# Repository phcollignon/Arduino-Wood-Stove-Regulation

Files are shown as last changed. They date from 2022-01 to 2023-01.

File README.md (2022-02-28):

# Arduino Wood Stove Regulator

## Introduction

It is a hard job to control the air supply of a wood stove.

I built an automatic regulator that does this for you. It regulates the air supply according to the temperatures of the chimney.

Combustion is always optimal and you get the most calories from your firewood.

You receive a notification when a refill of wood is needed.

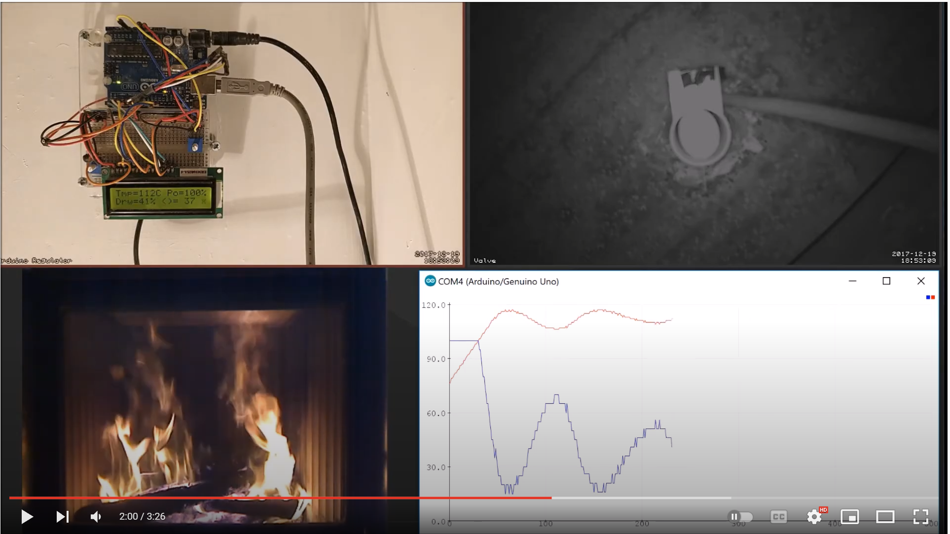
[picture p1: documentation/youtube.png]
Watch the video (https://youtu.be/uNl3eiWf07A)


At the end of the fire, the system automatically closes the air supply to prevent the stove from cooling too quickly.

***WARNING: always leave a minimum draft. Not supplying enough air to the stove is dangerous. It can produce lethal CO or an incomplete burn gas explosion.***

***Disclaimer: I am not responsible for the use of this project. By using this project, you assume all responsibility for its configuration, implementation, and use.***

## The regulation

The regulation is controlled by an Arduino UNO.

It is connected to :

* a termocouple (max6675).
* a servo motor to control the valve (small one TowerPro 9g SG90)
* a buzzer
* a LCD screen (16x2)
* a potentiometer to control manually the air supply.
* a reset button 
  
If the air supply is set to maximum, the Arduino goes into automatic mode and controls the valve based on the temperature measured by the thermocouple.

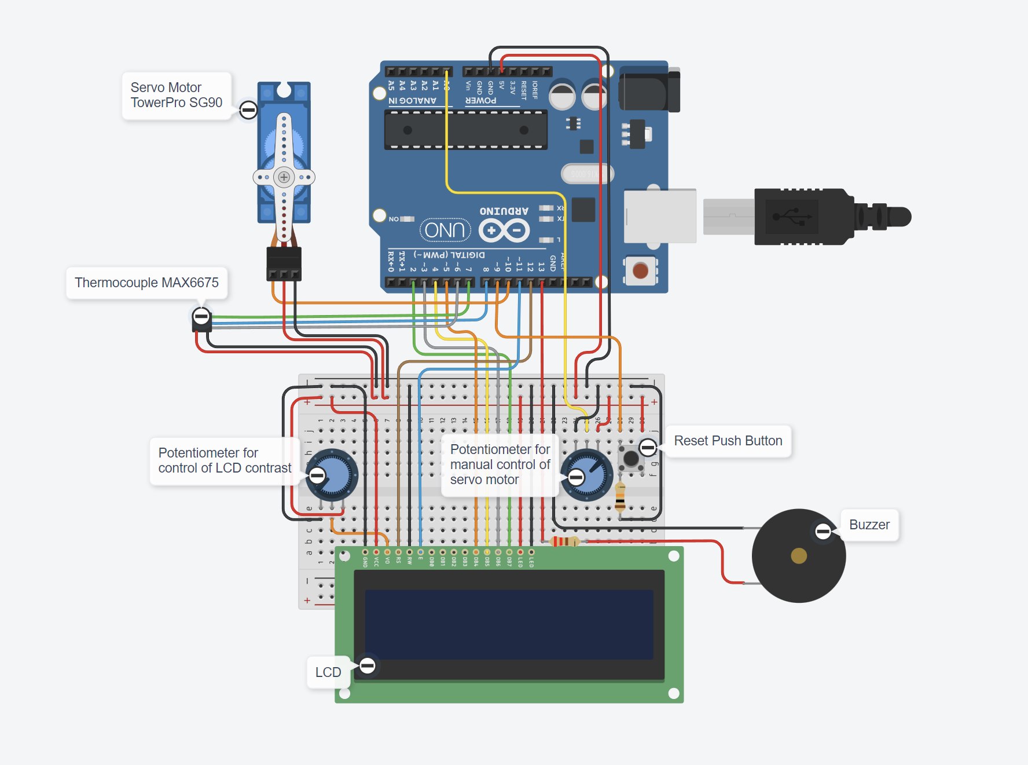
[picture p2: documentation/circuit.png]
circuit
 
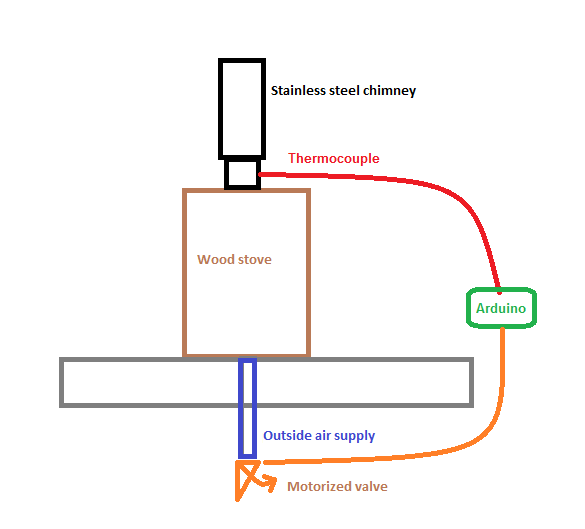
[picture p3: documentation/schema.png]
schema

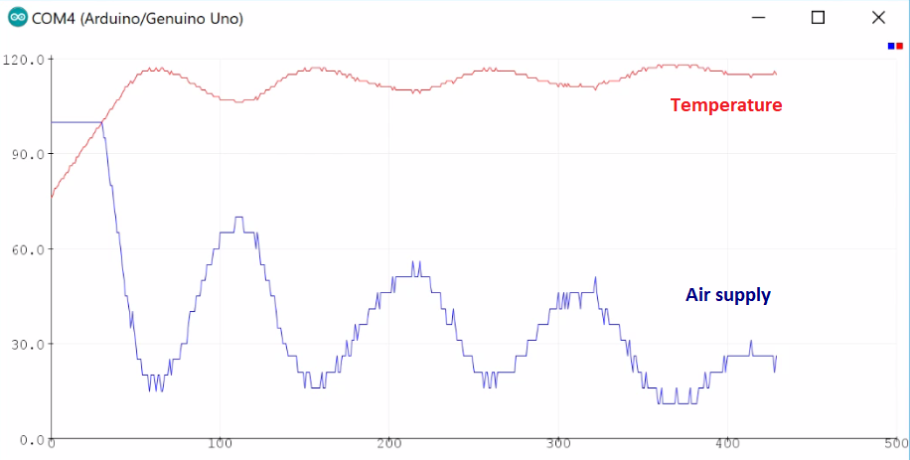
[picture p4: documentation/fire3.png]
regulation


## The code

The Arduino sketch implements a PID control that stabilizes the temperature.

The Arduino sketch is open source and available for download here : [stove-regulation.ino](https://github.com/phcollignon/Arduino-Wood-Stove-Regulation/blob/master/Arduino/stove-regulation.ino) , please read the header before using it.  

I use Adafruit's max6675 library, it can be installed from the Arduino IDE.

IMPORTANT : You first have to configure the properties and the PID values so that they match your project .. (see step : Test and configure regulation )

## The Thermocouple

The thermocouple is a MAX6675 type.

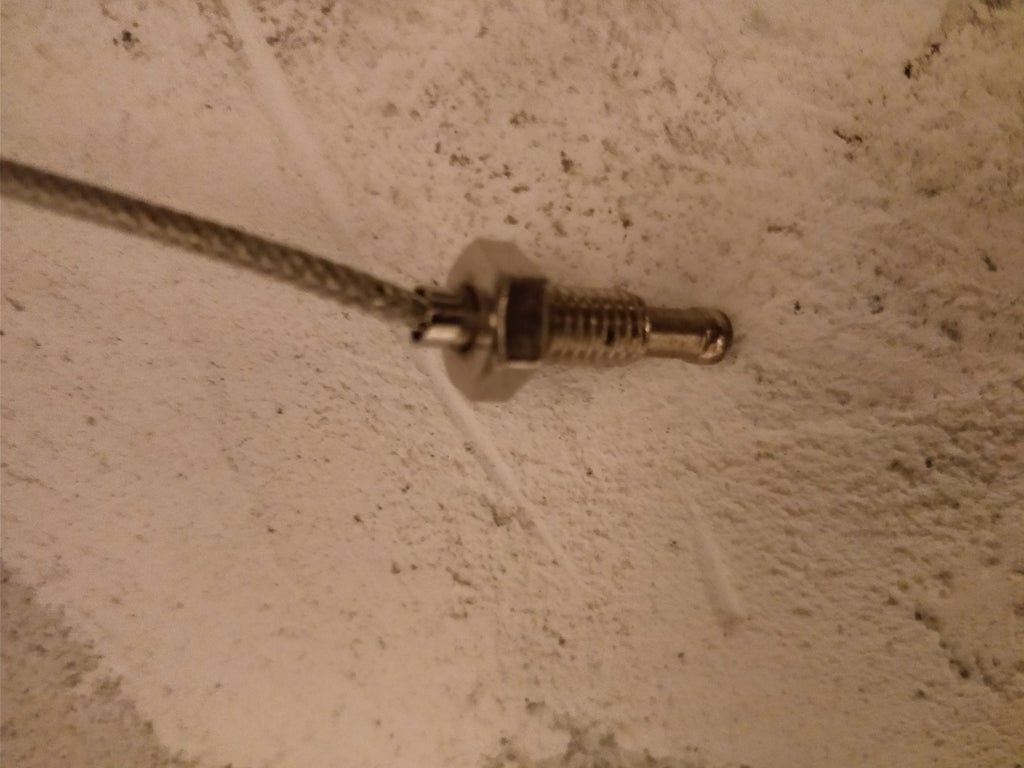
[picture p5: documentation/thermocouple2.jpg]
thermocouple


Connect a wire from your Arduino to somewhere you can measure chimney or stove temperature.

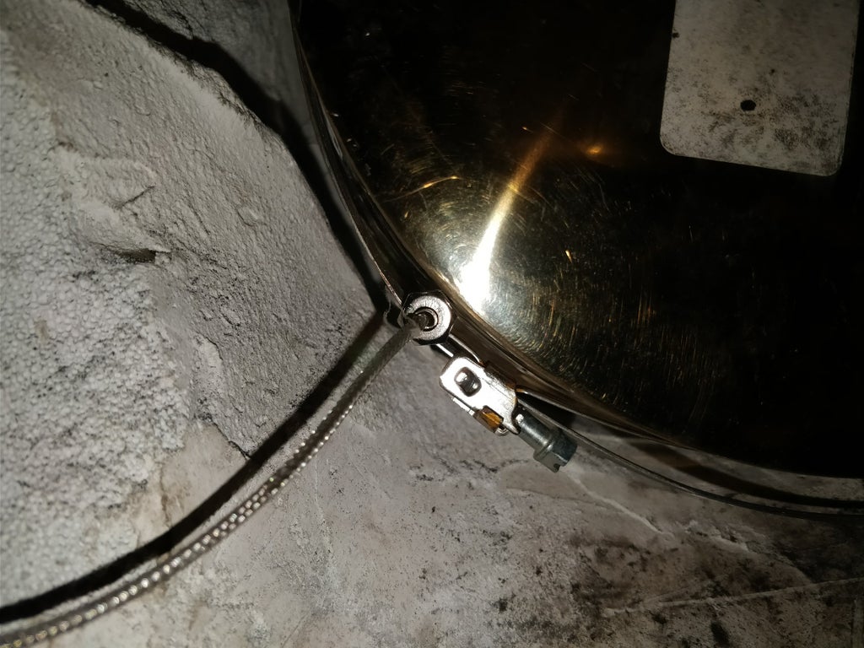
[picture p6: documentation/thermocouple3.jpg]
thermocouple


Connect the thermocouple and fix the end in contact with the uninsulated part of your stainless steel chimney or in contact with the external part of the stove. Not inside the fireplace!!

As told above, I use Adafruit's library. You can install the Adafruit's library from Arduino's IDE.

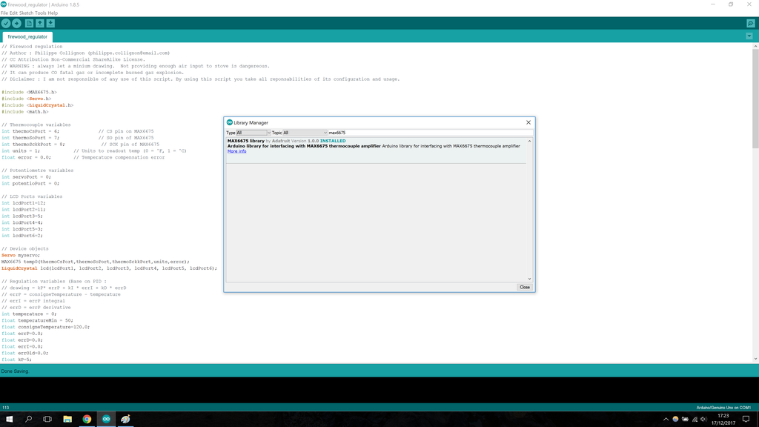
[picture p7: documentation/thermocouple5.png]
thermocouple


## The Valve

The case of the valve and servo is 3D printed.

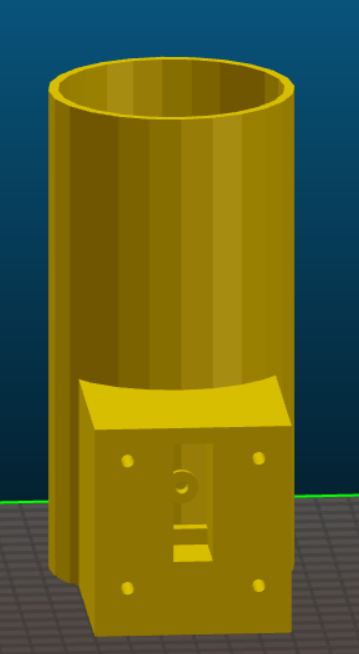
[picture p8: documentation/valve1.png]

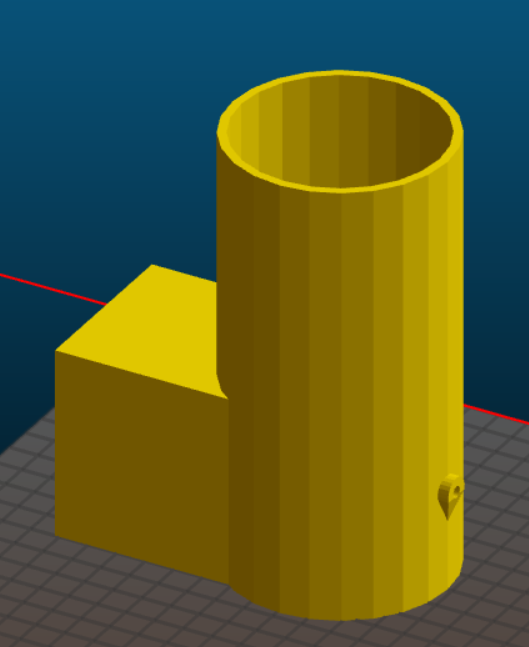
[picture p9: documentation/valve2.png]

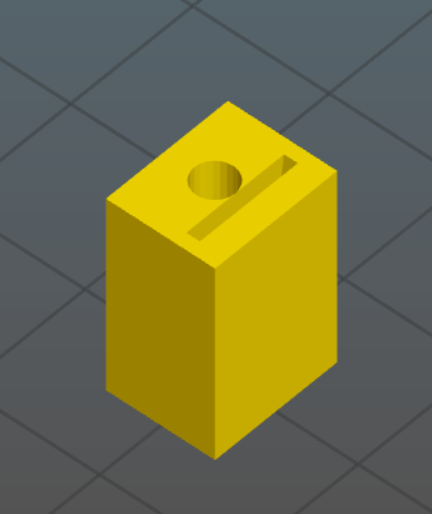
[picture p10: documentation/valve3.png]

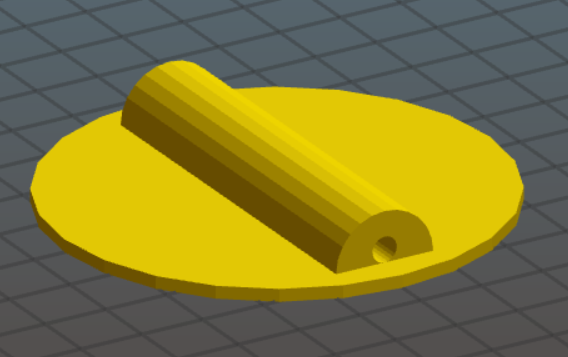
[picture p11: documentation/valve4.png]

cylindre
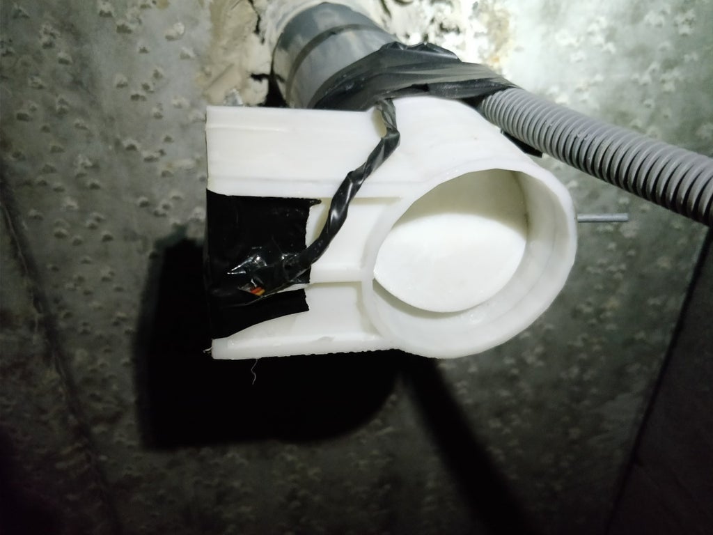
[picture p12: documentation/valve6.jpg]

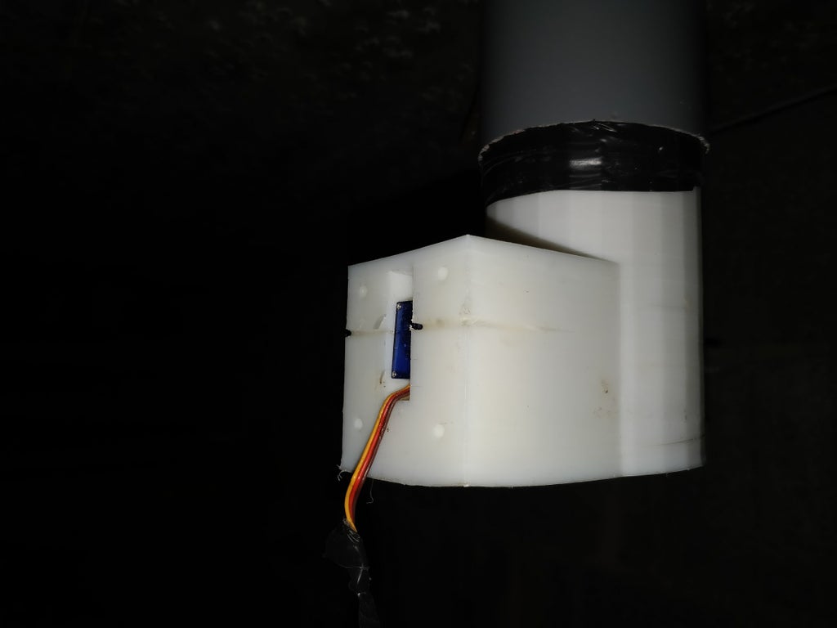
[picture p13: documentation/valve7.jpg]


The STL files are available for download.

* print the disc valve [disc](3DPrint/disc.stl)
* print the case with the cylinder [cylinder](3DPrint/cylindre.stl)
* print the servo-to-hinge connector [connector](3DPrint/connector.stl)
  
Please note that they are all printed in ABS, you might update printing size for other materials.

After initial configuration (see here below); you can fix the cylindre to the air supply. Connect a wire between the Arduino and the air supply.

Warning it must be an external air supply away from heat source !!

## The servo motor

The servo motor is a TowerPro SG90 type.

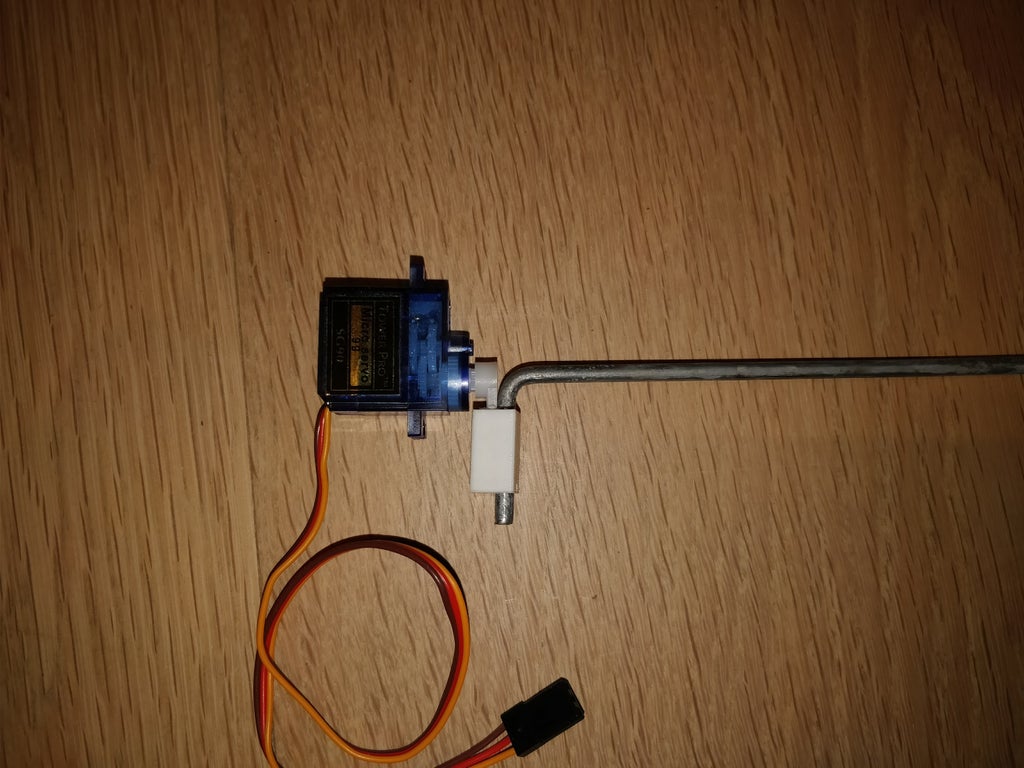
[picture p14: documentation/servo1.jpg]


Push a long hook inside the valve's hinge.
Connect the hook to the servo motor with the connector 3D printed part
Push the hook and the servo inside the case with the valve in place
Fix the valve on the hook, I drill three small holes and put super glue inside.
Check that the valve is turning without resistance (the servo is not powerfull..)

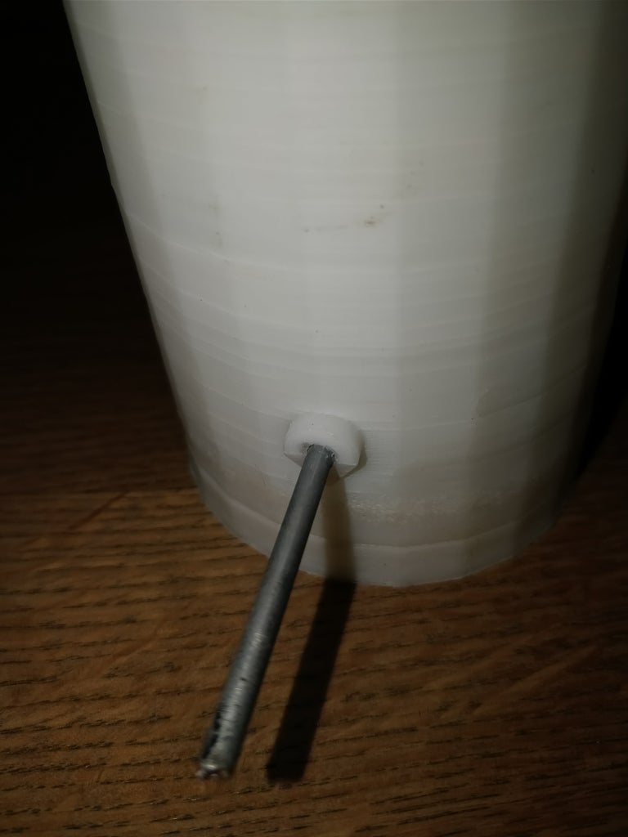
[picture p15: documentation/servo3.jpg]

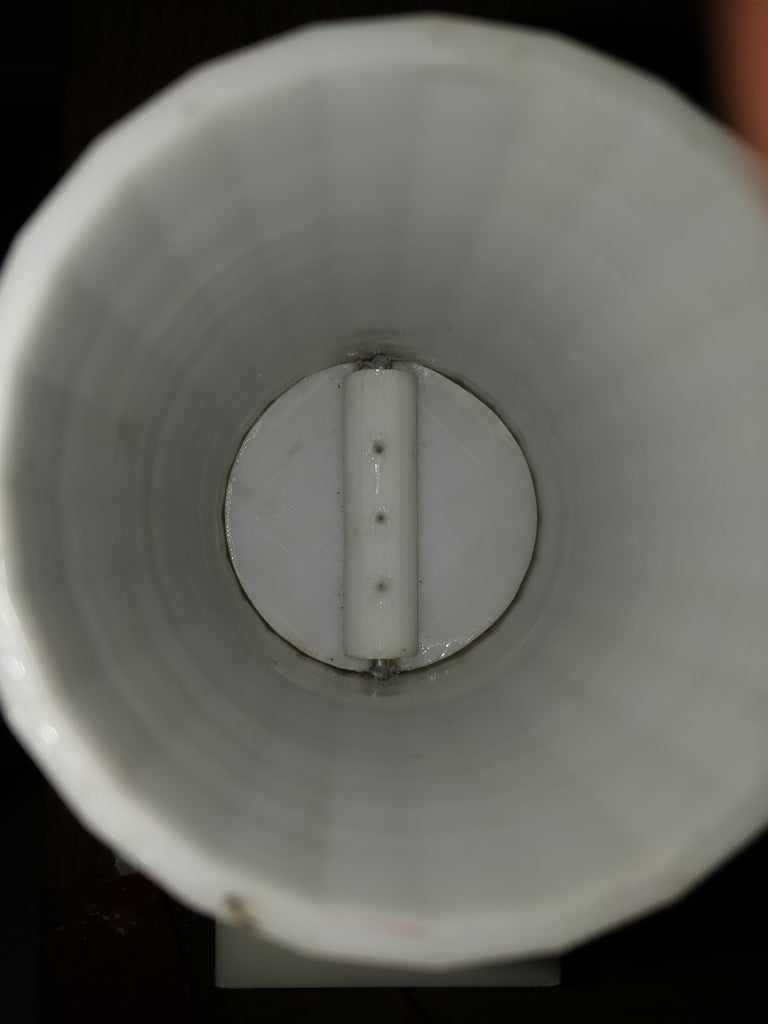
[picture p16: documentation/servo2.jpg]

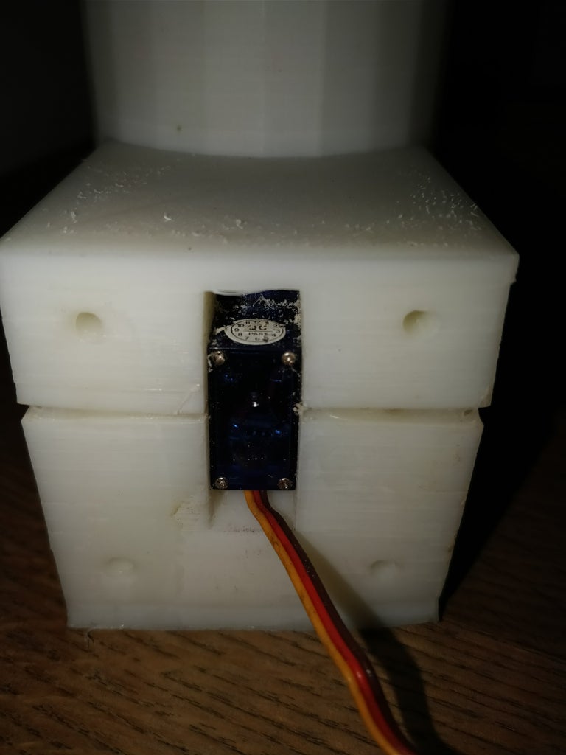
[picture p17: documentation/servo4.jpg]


The servo motor has to be calibrated with the two following variables :

* int angleCalibration = 90; // modify this value so that initial angle of the servo is 0° 
* float servoCalibration = 1;  // modify this value so that servo is at 90° when angle is 90°

## Regulation configuration

A regulation need some configuration, you may have to change the default parameters :

* float temperatureMin = 50; // under this temperature, the regulation starts an integral measure to estimate end or fire and close the valve

* float consigneTemperature=120.0; // the desired temperature measured by the thermocouple

* float kP=5; // P parameter of the PID regulation

* float kI=0.0005; // I parameter of the PID regulation

* float kD=0.00005; // D parameter of the PID regulation

* float refillTrigger = 5000; // refillTrigger used to notify need of a wood refill

* float closeTrigger = 15000; // closeTrigger used to close vlave at end of combustion and notifiy end of fire

* float potentioMax = 1023.0; // Potentiometre calibration

* int potentionRelMax = 80; // Potentiometre value above which the regulator runs in automatic mode

It is highly recommended to test the system before deploying it ..

Connect the thermocouple,
Upload the sketch to Arduino.
Connect the valve but do not connect it to the air supply yet.
Calibrate the zero angle of the servo motor.
First manually test the valve with the potentiometer
Then make a firewood and check the thermocouple and the valve behaviour (by simulating the air admission with your stove manual controller) To put the Arduino regulator in automatic mode, you have to put the potentiometer to 100%.

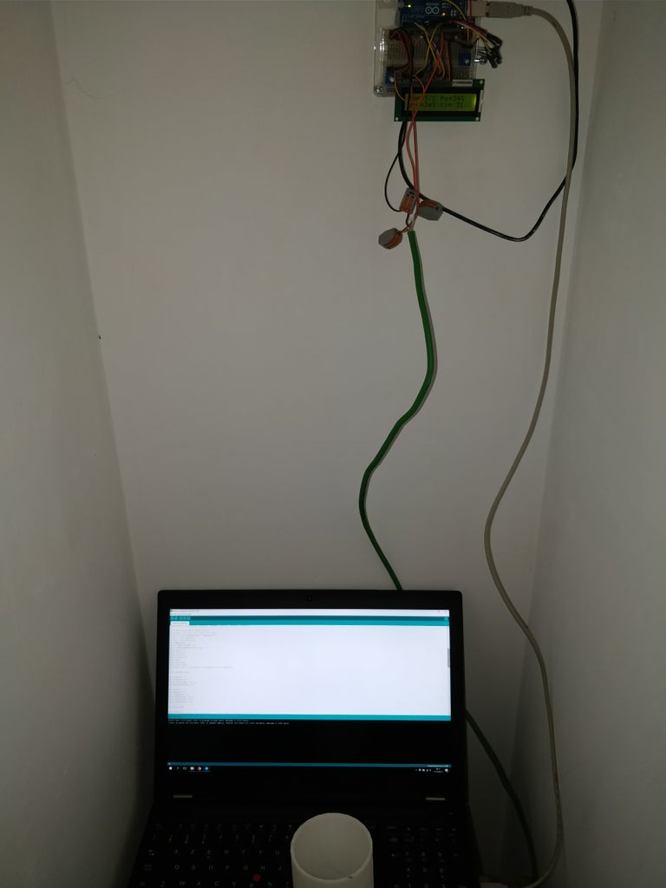
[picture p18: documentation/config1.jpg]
config1

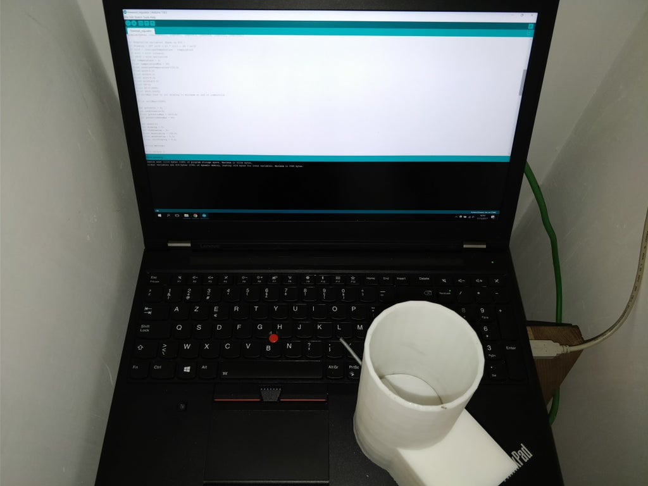
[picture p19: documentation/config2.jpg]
config1

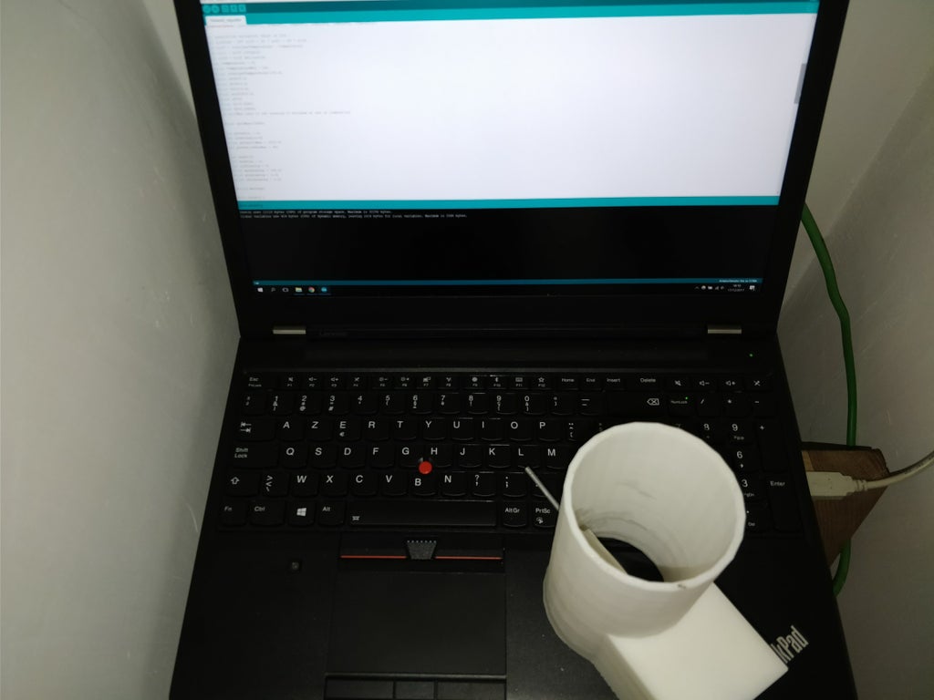
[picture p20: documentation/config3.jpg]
config1

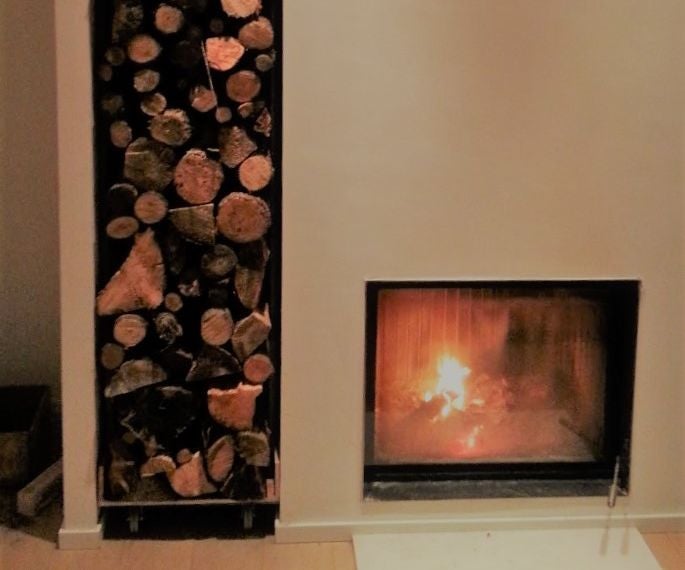
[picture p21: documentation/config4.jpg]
config1


## The notifications

There are two notifications that can be customized :

* "wood refill" notification
 When a wood refill notification occurs, you have to put some wood, the wood refill message is going to disappear when the temperature goes up the target temperature again.
* "end of fire" notification
When a fire end notification occurs the valve closes to keep the heat in the stove. You can press the reset button to open it again the next time you want to start a new fire.

Both notification are based on the integral of the PID to be more accurate (than notifications based on temperatures)

The trigger values must be configured in the arduino sketch. You have to tune them for your wood stove.
If your refill notification raises to early, just increase refillTrigger variable.

* float refillTrigger = 5000; // refillTrigger used to notify need of a wood refill
* float closeTrigger = 15000; // closeTrigger used to close vlave at end of combustion

The notification and buzzer frequency and delay can be configured in the arduino sketch.
Buzzer variables :

* int buzzerPort = 9; // Buzzer port
* int buzzerRefillFrequency = 2000; // Buzzer tone frequency for refill alarm
* int buzzerRefillRepeat = 3; // Number of refill alarm tones
* int buzzerRefillDelay = 1000; // Delay of refill alarm tone
* int buzzerCloseFrequency = 1000; // Buzzer tone frequency for end of fire valve close alarm
* int buzzerCloseRepeat = 2; // Number of tones for end of fire valve close alarm
* int buzzerCloseDelay = 2000; // Delay of tone for end of fire valve close alarm

## Light the fire

Be sure you configured and tested as explained in previous steps.

To start in automatic mode, put the right potentiometer to the maximum to the right (more than 80% clockwise)
Check the values on the LCD (angle should be 90°, and draft 100%)

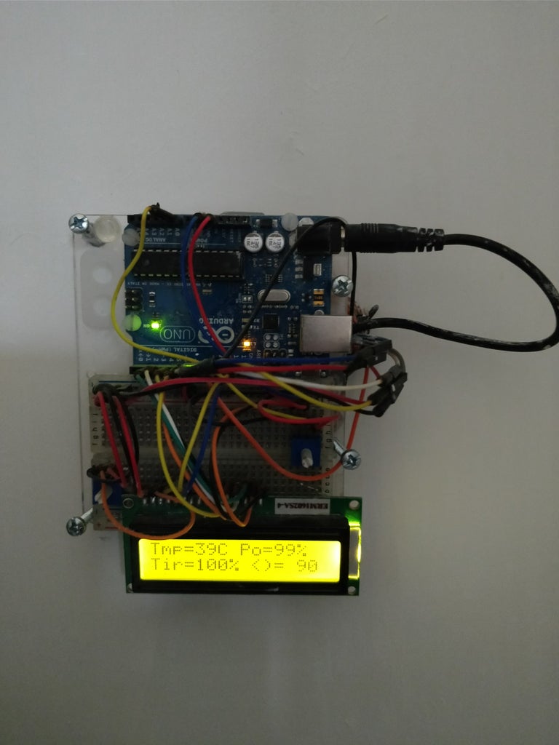
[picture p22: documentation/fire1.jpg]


Start a fire, check the temperature. When the temperature goes up the desired temperature (consigneTemperature in the sketch) the valve should close. If the fire becomes too weak, the valve should open. If the fire becomes too strong, the valve should close again. If something goes wrong, use the potentiometer below 80% to be in manual mode or use the manual control of your wood stove.

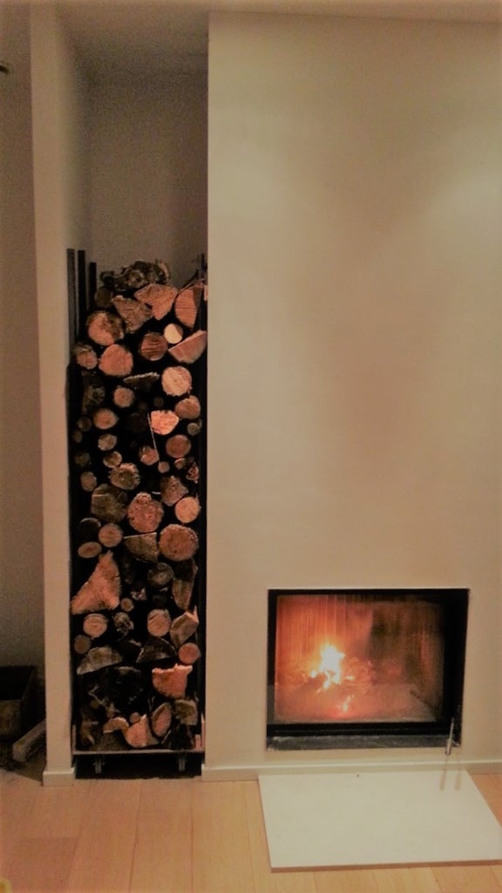
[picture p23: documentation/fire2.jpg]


You can get some nice PID curves by getting the values with Arduino serial port and plotting them. (In red the valve angle, in blue the temperature)

config1

At the end of the fire, the system automatically close the air supply to prevent the stove to cool down to fast.

To restart the system, press the reset button or  turn the potentiometer to zero then back to maximum value. 

***ATTENTION: always leave a minimum draft. Not supplying enough air to the stove is dangerous. It can produce deadly CO gas or an incomplete burn gas explosion.
Disclaimer: I am not responsible for the use of this project. By using this project, you assume all responsibility for its configuration, implementation, and use.***

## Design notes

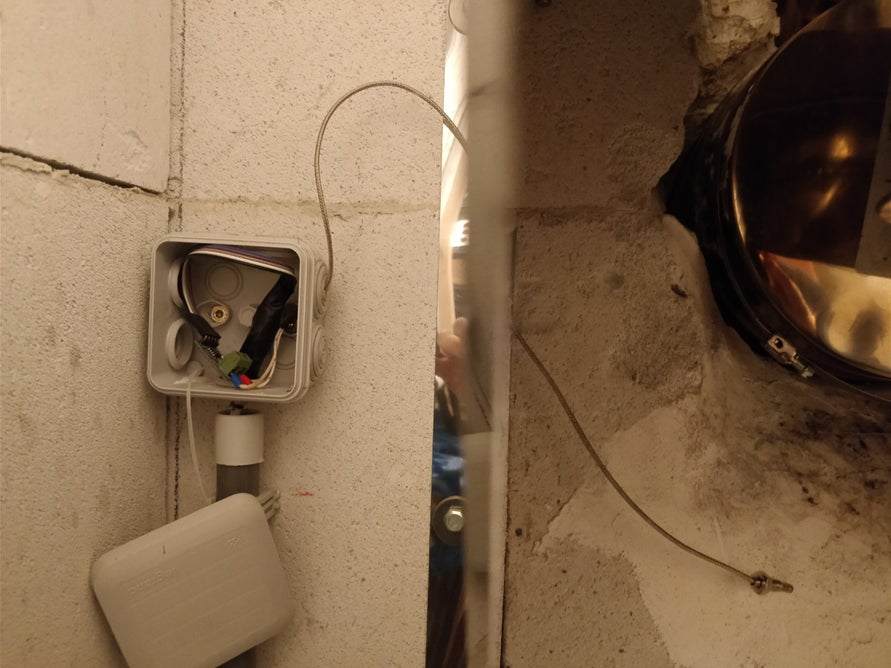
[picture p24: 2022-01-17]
documentation/thermocouple1.jpg

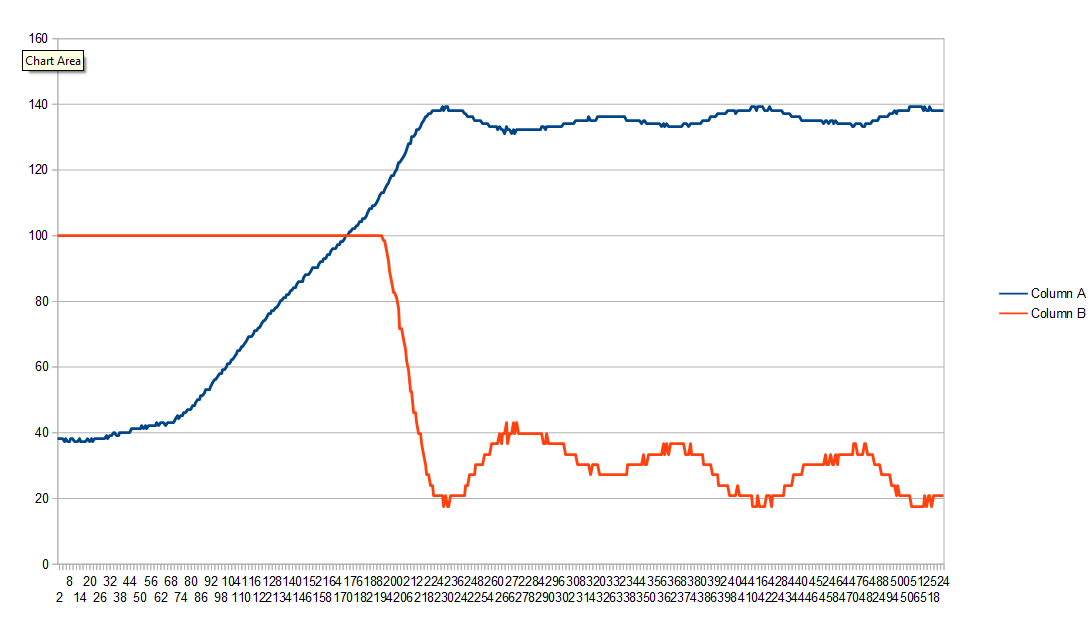
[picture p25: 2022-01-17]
documentation/Capture2.PNG

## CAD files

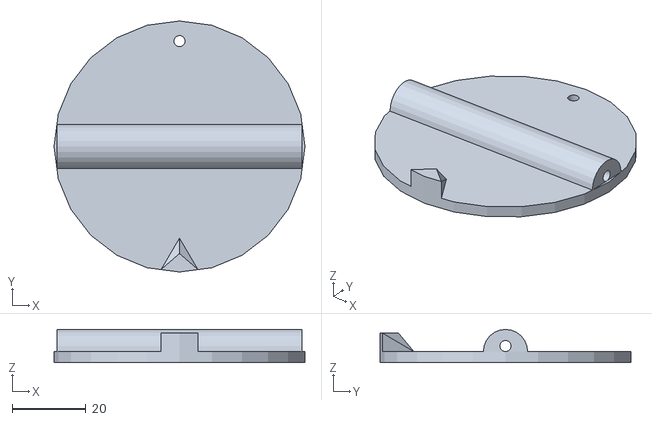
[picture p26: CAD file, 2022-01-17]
3DPrint/disc.stl
68.0 x 68.0 x 9.00

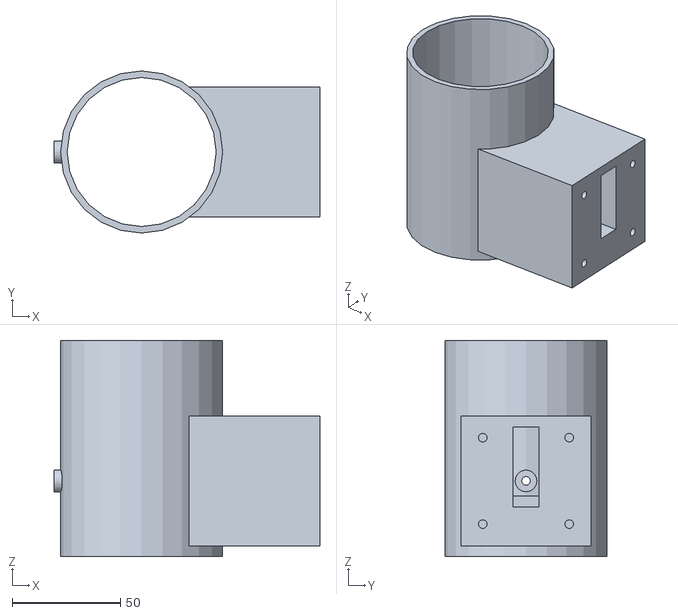
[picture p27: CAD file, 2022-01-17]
3DPrint/cylindre.stl
123.1 x 75.0 x 100.0

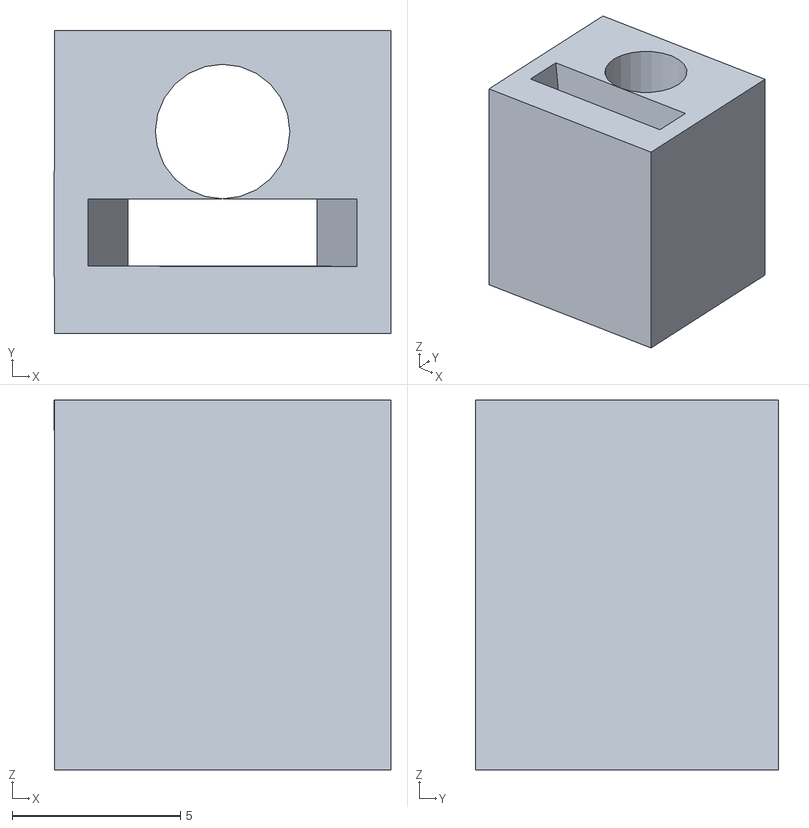
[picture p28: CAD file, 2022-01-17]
3DPrint/connector.stl
10.0 x 9.00 x 11.0

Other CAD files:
3DPrint/connector.skp
3DPrint/cylindre.skp
3DPrint/cylindre_v1.skp
3DPrint/disk.skp
3DPrint/disk_v1.skp

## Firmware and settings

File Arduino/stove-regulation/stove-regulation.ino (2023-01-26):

// Firewood regulation
// Author : Philippe Collignon (philippe.collignon@email.com)
// CC Attribution Non-Commercial ShareAlike License.
// WARNING : always let a minimum draft.
// Not providing enough air supply to stove is dangerous.  It can produce fatal CO gaz or incomplete burned gaz explosion.
// Disclaimer : I am not responsible of any use of this script. By using this script you take all responsability of its configuration and usage.

#include <max6675.h>
#include <Servo.h>
#include <LiquidCrystal.h>
#include <math.h>

// Thermocouple variables
int thermoCsPort = 6;   // CS pin on MAX6675
int thermoSoPort = 7;   // SO pin of MAX6675
int thermoSckkPort = 8; // SCK pin of MAX6675
int units = 1;          // Units to readout temp (0 = ˚F, 1 = ˚C)
float error = 0.0;      // Temperature compensation error

// Buzzer variables
int buzzerPort = 13;              // Buzzer port
int buzzerRefillFrequency = 2000; // Buzzer tone frequency for refill alarm
int buzzerRefillRepeat = 3;       // Number of refill alarm tones
int buzzerRefillDelay = 1000;     // Delay of refill alarm tone
int buzzerCloseFrequency = 1000;  // Buzzer tone frequency for end of fire valve close alarm
int buzzerCloseRepeat = 2;        // Number of tones for end of fire valve close alarm
int buzzerCloseDelay = 2000;      // Delay of tone for end of fire valve close alarm

// Reset button variables
int resetPort = 9;

// Potentiometre variables
int servoPort = 0;
int potentioPort = 0;

// LCD Ports variables
int lcdPort1 = 12;
int lcdPort2 = 11;
int lcdPort3 = 5;
int lcdPort4 = 4;
int lcdPort5 = 3;
int lcdPort6 = 2;

// Device objects
Servo myservo;
int angleCalibration = 95;                                        // modify this value so that initial angle of the servo is 0°
float servoCalibration = 1;                                       // modify this value so that servo is at 90° when angle is 90°
MAX6675 thermocouple(thermoSckkPort, thermoCsPort, thermoSoPort); //,units,error);
LiquidCrystal lcd(lcdPort1, lcdPort2, lcdPort3, lcdPort4, lcdPort5, lcdPort6);

// Regulation variables (Base on PID :
// draft = kP* errP + kI * errI + kD * errD
// errP = consigneTemperature - temperature
// errI = errP integral
// errD = errP derivative
int temperature = 0;
float temperatureMin = 50;         // under this temperature, the regulation starts an integral measure to estimate end or fire and close the valve
float consigneTemperature = 130.0; // the desired temperature measured by the thermocouple
float errP = 0.0;
float errD = 0.0;
float errI = 0.0;
float errOld = 0.0;
float kP = 5;       // P parameter of the PID regulation
float kI = 0.0005;  // I parameter of the PID regulation
float kD = 0.00005; // D parameter of the PID regulation

float refillTrigger = 7500; // refillTrigger used to notify need of a wood refill
float closeTrigger = 15000; // closeTrigger used to close vlave at end of combustion

int potentio = 0;
int oldPotentio = 0;
float potentioMax = 1023.0; // Potentiometre calibration.
int potentioRelMax = 80;    // Potentiometre value above which the regulator runs in automatic mode

int reset = HIGH;

int angle = 0;
int draft = 0;
int oldDraft = 0;
float maxDraft = 100.0;
float minDraft = 5.0;
float zeroDraft = 0.0;

String messageTmp;
String messageDrf;

boolean closeBuzzer = true;
boolean refillBuzzer = true;

long debounceTime = 0;
long debounceDelay = 50;
int lastResetState = LOW;
int resetState = LOW;

void setup()
{
  Serial.begin(9600);
  myservo.attach(10);
  myservo.write(0);
  myservo.detach();
  lcd.begin(16, 2);
  pinMode(buzzerPort, OUTPUT);
  pinMode(resetPort, INPUT);
}

void loop()
{

  temperature = thermocouple.readCelsius() - 60; //-32)*5/9;
  potentio = analogRead(potentioPort);
  reset = digitalRead(resetPort);

  delay(500);
  if (temperature == -1)
  {
    Serial.println("Thermocouple Error!!"); // Temperature is -1 and there is a thermocouple error
  }
  else
  {
   

    // Read potentiometer
    potentio = (potentioMax - potentio) * 100 / potentioMax;

    if ((potentio < potentioRelMax))
    {
      // Potentiometre regulation
      draft = round(potentio * maxDraft / 100);
      errI = 0;
      errD = 0;
      closeBuzzer = true;
      refillBuzzer = true;

      messageDrf = "Drf=" + String(round(draft / maxDraft * 100)) + "%" + " <)= " + String(round(draft * 90 / maxDraft)) + "";
    }
    else
    {
      if (errI < closeTrigger)
      {
        // PID regulation
        errP = consigneTemperature - temperature;
        errI = errI + errP;
        errD = errP - errOld;
        draft = kP * errP + kI * errI + kD * errD;
        errOld = errP;

        // Limit values to physical constraints ..
        if (draft < minDraft)
          draft = minDraft;
        if (draft > maxDraft)
          draft = maxDraft;

        // Close end fire
        if (errI >= closeTrigger)
          errI = closeTrigger;
        if (temperature < temperatureMin)
          errI = 0;
        if (errI >= closeTrigger)
          draft = zeroDraft;

        messageDrf = "Drf=" + String(round(draft / maxDraft * 100)) + "%" + " <)= " + String(round(draft * 90 / maxDraft)) + "";
        // Refill Alarm
        if (errI > refillTrigger)
        {
          messageDrf = "Please refill !!";
          if (refillBuzzer)
          {
            for (int i = 0; i < buzzerRefillRepeat; i++)
            {
              tone(buzzerPort, buzzerRefillFrequency);
              delay(buzzerRefillDelay);
              noTone(buzzerPort);
              delay(buzzerRefillDelay);
            }
            refillBuzzer = false;
          }
          if (temperature > consigneTemperature)
          {
            errI = 0;
            errD = 0;
            refillBuzzer = true;
          }
        }
      }

      else
      {
        // Close Valve if end of combustion
        messageDrf = "Fire End.  <)= " + String(round(draft * 90 / maxDraft)) + "";

        if (closeBuzzer)
        {
          for (int i = 0; i < buzzerCloseRepeat; i++)
          {
            tone(buzzerPort, buzzerCloseFrequency);
            delay(buzzerCloseDelay);
            noTone(buzzerPort);
            delay(buzzerCloseDelay);
          }
          closeBuzzer = false;
        }
      }
    }

     // Handle reset button with debounce support
   
        if (reset == HIGH)
        {
          draft = 100;
          errI = 0;
          errD = 0;
          closeBuzzer = true;
          refillBuzzer = true;
          messageDrf = "Reset ... ";
          delay(1000);
        }
     

    // Display message on LCD
    lcd.clear();
    lcd.setCursor(0, 0);
    messageTmp = "Tmp=" + String(temperature) + "C" + " Po=" + round(potentio) + "%";
    lcd.print(messageTmp);
    lcd.setCursor(0, 1);
    lcd.print(messageDrf);
    // Serial Plotter
    // Serial.print(round(draft/maxDraft* 100));
    // Serial.print(" ");
    // Serial.println(temperature);

    // Turn servo only for 5° delta
    if (abs(oldDraft - draft) > 5)
    {
      lcd.print(" x");
      delay(500);
      myservo.attach(10);
      angle = angleCalibration + (draft * 90 / maxDraft * servoCalibration);
      myservo.write(angle);
      delay(500);
      myservo.detach();

      oldPotentio = potentio;
      oldDraft = draft;
      
    }
    delay(1500);
  }
}

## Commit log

2022-01-17 Drawing to draft wrong translation
    [stove-regulation.ino]
2023-01-26 Restet button support
2023-01-26 Reset button support
